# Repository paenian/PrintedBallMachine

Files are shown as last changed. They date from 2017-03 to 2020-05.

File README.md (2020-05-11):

The PrintedBallMachine!

Herein are some tips for working with the printed ball machine - making your own modules, first, and later making your own parts.

# Video!
https://www.youtube.com/watch?v=hsoqrZ5NXNs

# Rough Idea
The PBM is a marble machine that utilized pegboard for its vertical structure.  In order to make modular units, the pegboard is cut into 12" sections, with defined inlet and exit for linking together.  The machines are standardized on 5/8" steel ball bearings, because steel is satisfying.  This is the same size as the common glass marble, however there is much more variation in marbles than there are in ball bearings.

The Printed Ball Machine is designed in [OpenSCAD](http://www.openscad.org/), the programmer's solid modeler.

# Common Parts (vitamins, in the RepRap lingo - stuff you'll need to buy)
* Pegboard - 1" holes, 1/4" thick.  This is the 'heavy duty' pegboard, usually just brown hardboard.  Thinner stuff works, but not as well.  Generally sold in 2 foot by 4 foot sections - for modules, cut to 12" square.  Available at Home Depot/Lowes type stores - and they'll cut it if you ask nicely.
  * [home depot](https://www.homedepot.com/p/Triton-1-4-in-x-1-8-in-Heavy-Duty-Brown-Pegboard-Wall-Organizer-Set-of-4-TPB-4BR/205196091)
* 5/8" Steel Ball Bearings - I get mine from McMaster Carr, but anything'll work.
* Pololu plastic gear motors - I standardized on this motor because it fits nicely in a 1" space, has a right-angle drive and decent torque, plus runs off 5v easily.
  * [Pololu Plastic Gearmotor](https://www.pololu.com/product/1120)
  * You can get less-geared versions for faster motors, too.
* USB Charger and Cables
  * The motors are nominally 6v, but run fine (a little slower) at 5v - so we cut up old or cheap USB cables to power them.
  * You can also buy USB splitters, to minimize the number of chargers needed - two motors per amp is safe, in practice 4 seems to work fine.
* M3x12mm flat-head screws - two to hold each motor on, no tapping :-)
* #3 by 3/8" flat wood screws - used to hold parts onto the motor, fits perfectly into its D-shaft, no tapping.
* 12" x 3/8" wooden dowels - to make a single-module with ball recirculation.

# Getting Started
To get started, you need a pegboard, a motor or two, and a 3D printer. To make life easier, we've broken the parts into modules - 12"x12" units that can be linked together.  A module is not complete; it requires the addition of feet and a ball return option - either wooden dowels to recirculate around the back, straight peg clamps to attach it to another adjacent module, 180 degree ball returns to mate it to a second module behind it or 90 degree ball returns to turn it into a square.

I think the best unit is actually two modules back-to-back - these can be recirculated simply, and joined by removing the recirculators and lining them up.  There are three ready modules:

[Stair Lifter Module](stair_lifter_module)

[Bearing Lifter Module](bearing_lifter_module)

[Screw Lifter Module](screw_lifter_module)

# Common Parts for Printing: The Standard Module
There are many standard parts in the [parts](parts) subfolder; in general modules will utilize many of these common components, i.e. feet, handles, pegs, ball returns, and simple sloped modules.  Then, each module will have a small number of largely unique parts, for its lifting and transporting mechanism.  A completed module will have a parts list divided into unique and standard, so it's easy to print and assemble it all :-)

# Tracks
The [tracks](tracks) subfolder contains a set of simple track modules, which can all carry the marble a certain number of spaces while dropping one space.  These can be used in modules directly, as glue logic basically - if you don't want to design a crazy exotic drop, or need a long ramp, see here.

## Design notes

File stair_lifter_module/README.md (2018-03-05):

# Stair Lifter!

A marble machine module that uses a stair-step mechanism on a cam.  The actual lifter consists of three parts:
# Unique Parts
* sl_inlet.stl - The back set of stairs, doubles as the outlet.  Recommended print in PLA
* sl_stairs.stl - The front, moving set of stairs - rides up and down on the cam.  Again, recommend PLA for easy sliding.
* sl_cam.stl - Oval to lift and lower the stairs - attaches to the motor which is mounted on the sl_inlet.

The module is finished off with a wide slope to drop the ball bearings back down:
# Track
* wide_slope.stl - found in the [tracks](../tracks) folder

## Assembly
To complete the assembly, you'll need a bunch of printed pegs, feet, and one finishing style.

### Finishing
* Straight Clamps - connect to module left and right
* Dowel Returns - recirculate balls back to ourselves
* 180 degree - link two modules
* 90 degree - turn the corner

## Double Module
marble enters in at mid-height, exits the same height.  Requires another similar module and two ball_return_180.stl from the [parts](../parts) folder.

 Uniques
* sl_inlet.stl - The back set of stairs, doubles as the outlet.  Recommended print in PLA
* sl_stairs.stl - The front, moving set of stairs - rides up and down on the cam.  Again, recommend PLA for easy sliding.
* sl_cam.stl - Oval to lift and lower the stairs - attaches to the motor which is mounted on the sl_inlet.

### Tracks
* wide_slope.stl - found in the [tracks](../tracks) folder

### Standard Parts
* 2 stand.stl - and note that the feet are on columns 2 and 12, counting from 1 to 12, i.e. we skip the first column.  Also, the longer part of the foot is to the front of the module.
* 13 peg_tpu.stl - printed in TPU, or use the PETG files printed in PETG.
  * 4 for the legs, 4 for the wide slope, 5-ish for the stair inlet.

### Vitamins
* 12"x12" square of 1/4" pegboard
* 2 M3x12mm flat-head screws - to attach the motor
* 1 #3 by 3/8" flat-head wood screws - to attach the sl_cam.stl to the motor shaft
* 1 [Pololu Plastic Gearmotor](https://www.pololu.com/product/1120)
* USB charger/cable/5v supply
  * Note that the motor can turn in either direction in this module.

## Linking Double Modules
To link two standard double modules, double the parts above or use a different module, and add: 

## Parts
* 2 ball_return_180.stl - turn the balls around at the ends
* 6 peg_tpu.stl - to hold the ball returns on
* 1 double_handle.stl - to rigidly affix the two pegboards to eachother
* 2 M5x60mm screws - attach the handle
* 2 M5 nuts
* 4 M5 washers

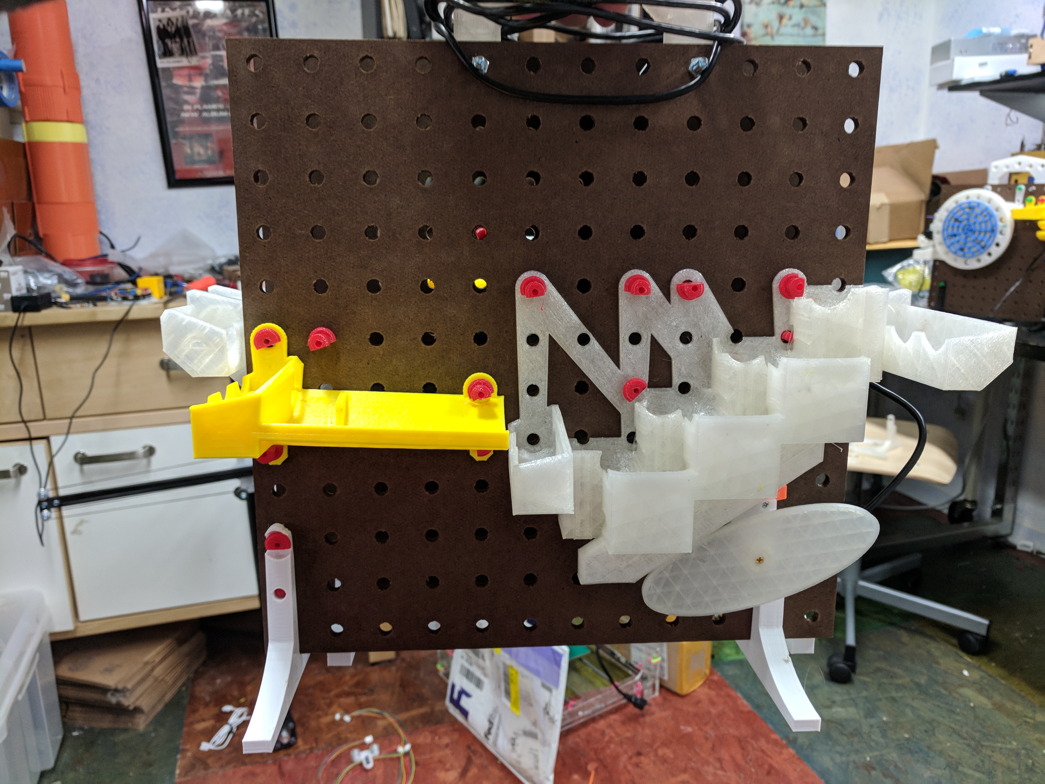
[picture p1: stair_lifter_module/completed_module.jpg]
Picture of the finished ball machine module Here's a completed double module, ready to recirculate.


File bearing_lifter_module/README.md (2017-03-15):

# Bearing Lifter
This is a lifter module, utilizing a print-in-place bearing.

Mechanical Parts:
1 motor
2 M5 screws and nuts for the handle
2 M3 screws to attach the motor
1 M3 screw to attach the guard

Parts to Print:
1 * bl_inlet.stl - marbles go in; also mounts the motor & bearing.
1 * bl_outlet.stl - marbles come out.
1 * bl_lift_gear.stl - the big bearing
1 * bl_drive_gear.stl - drive gear, attaches to the motor
1 * bl_guard.stl - finger guard, cuz the bearing's got ouchy torque
1 * bl_spiral.stl - a simple spiral drop.

Standard Parts
1 * stand_left.stl - pegboard stand
1 * stand_right.stl - pegboard stand
1 * handle.stl - to carry the pegboard
1 * breturn_inlet.stl - ball return!
1 * breturn_outlet.stl - ball return!
2 * breturn_peg.stl - special peg for the return
3 * peg_1x.stl - 1" peg
4 * peg_2x.stl - 2" peg
4 * peg_3x.stl - 3" peg

Notes:
Motor direction matters!
bl_inlet uses long pegs where it can.
You need a sideways support peg for the bl_outlet, under the fang-like curve.

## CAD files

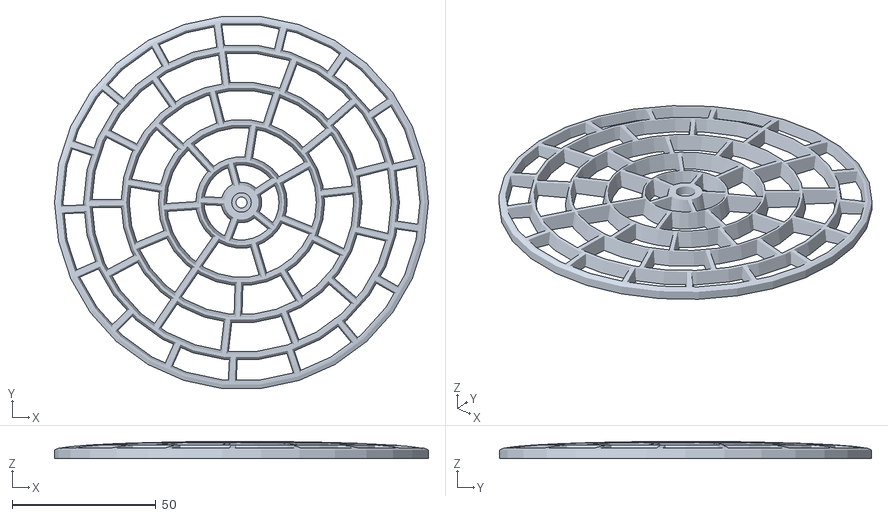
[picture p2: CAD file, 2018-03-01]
bearing_lifter_module/bl_guard.stl
130.0 x 129.3 x 5.98

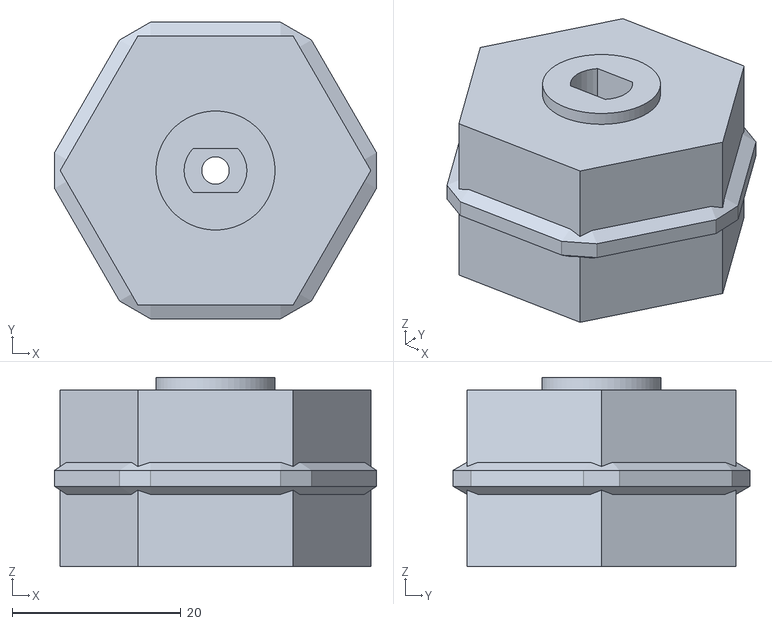
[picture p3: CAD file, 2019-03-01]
chain_lifter/cl_drive_gear.stl
38.1 x 35.2 x 22.4

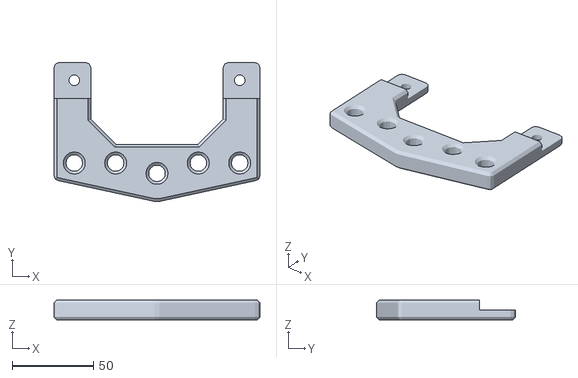
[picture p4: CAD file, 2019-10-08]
parts/handle.stl
126.5 x 85.2 x 12.2

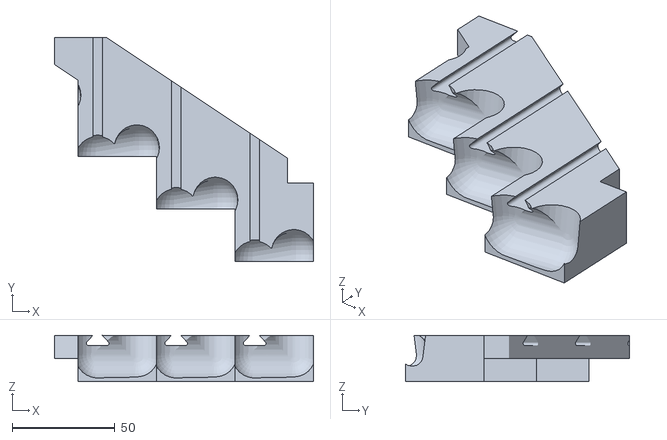
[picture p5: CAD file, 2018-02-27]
stair_lifter_module/sl_stairs.stl
125.7 x 108.5 x 22.4

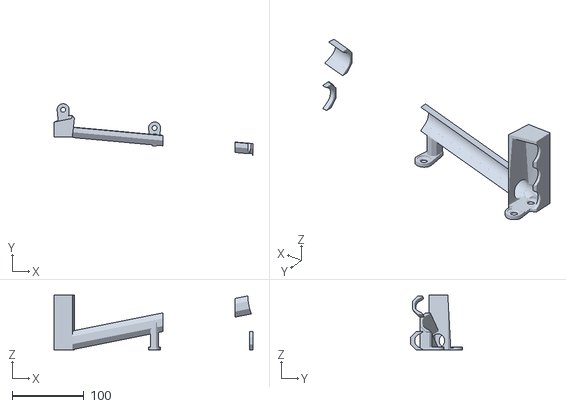
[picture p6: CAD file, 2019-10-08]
tracks/offset_slope_6.stl
276.4 x 71.6 x 76.2

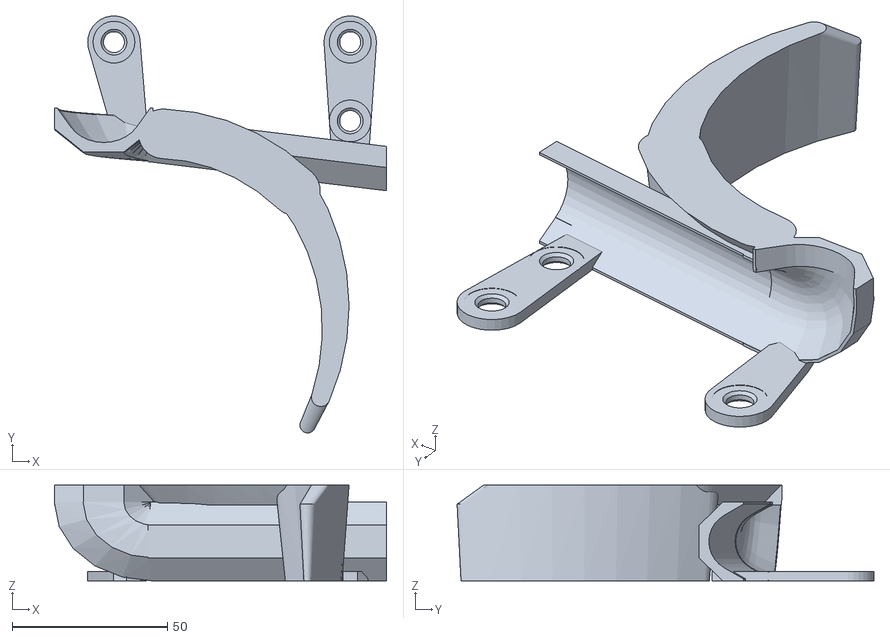
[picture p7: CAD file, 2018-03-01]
bearing_lifter_module/bl_outlet.stl
107.1 x 134.5 x 30.9

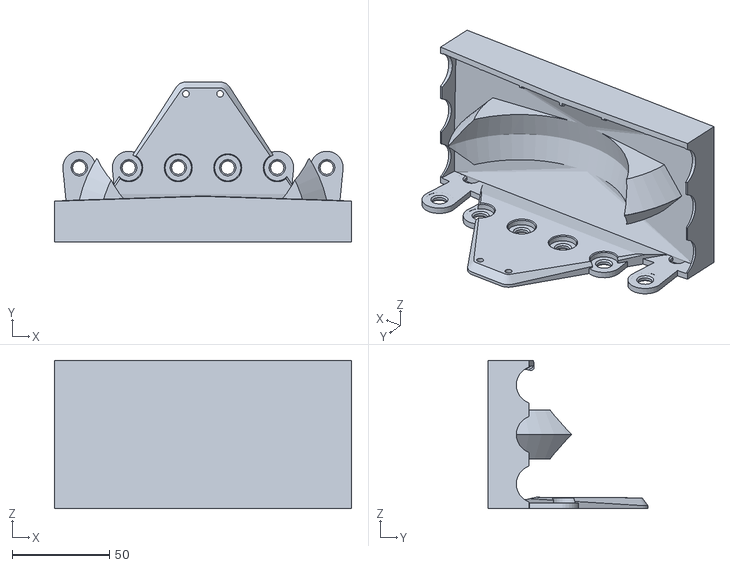
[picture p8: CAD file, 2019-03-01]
chain_lifter/cl_inlet.stl
152.4 x 82.1 x 76.2

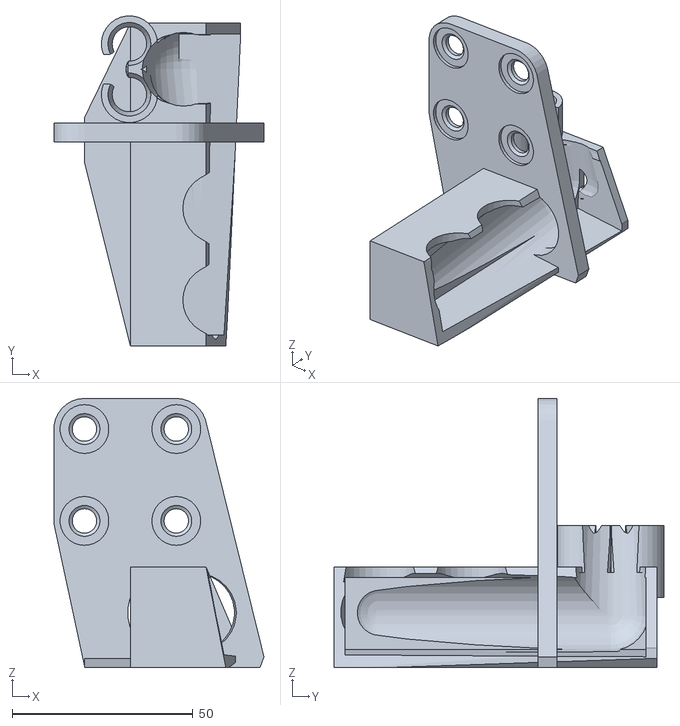
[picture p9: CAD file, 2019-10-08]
parts/ball_return_inlet_2.stl
58.1 x 91.2 x 74.4

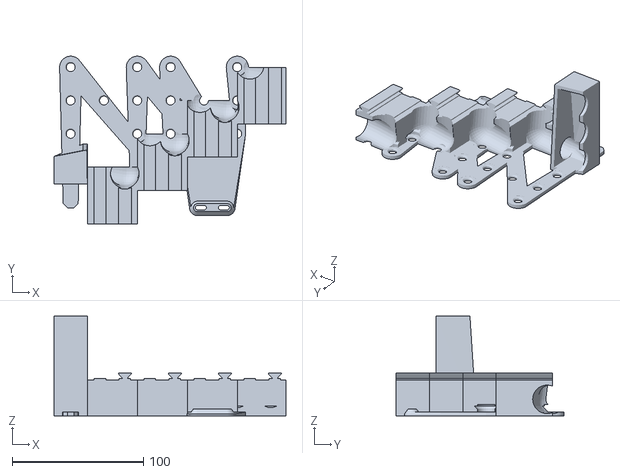
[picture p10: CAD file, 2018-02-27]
stair_lifter_module/sl_inlet.stl
176.8 x 127.7 x 76.2

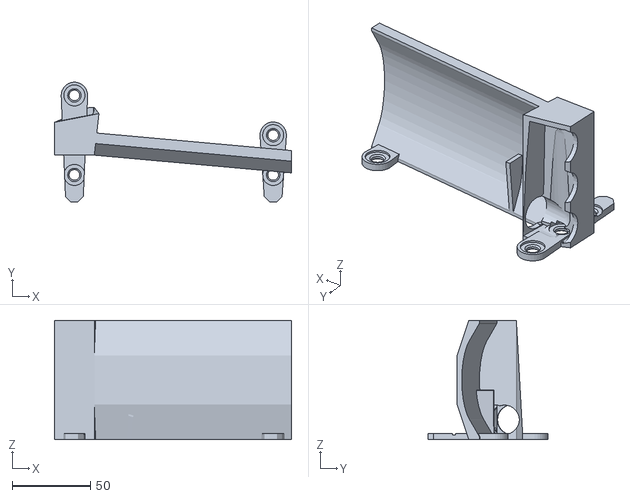
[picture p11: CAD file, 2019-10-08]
tracks/wide_slope_6.stl
151.4 x 76.4 x 76.2

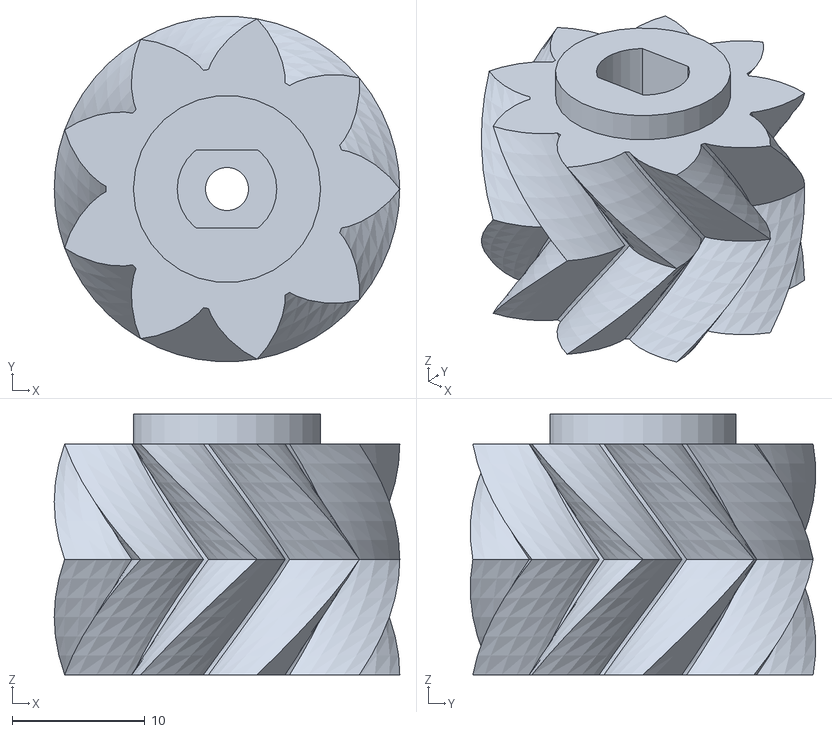
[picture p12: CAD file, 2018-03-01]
bearing_lifter_module/bl_drive_gear.stl
26.0 x 26.0 x 19.6

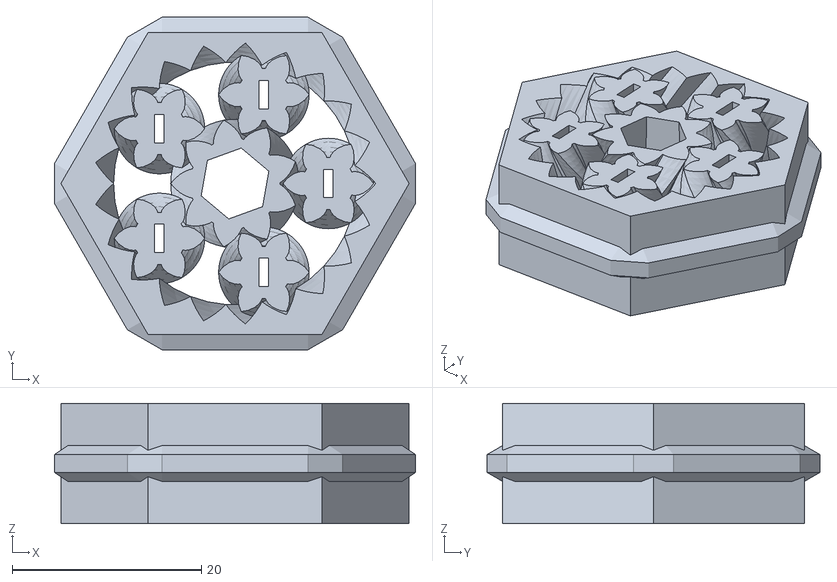
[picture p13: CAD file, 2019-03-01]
chain_lifter/cl_idler_gear.stl
38.1 x 35.2 x 12.7

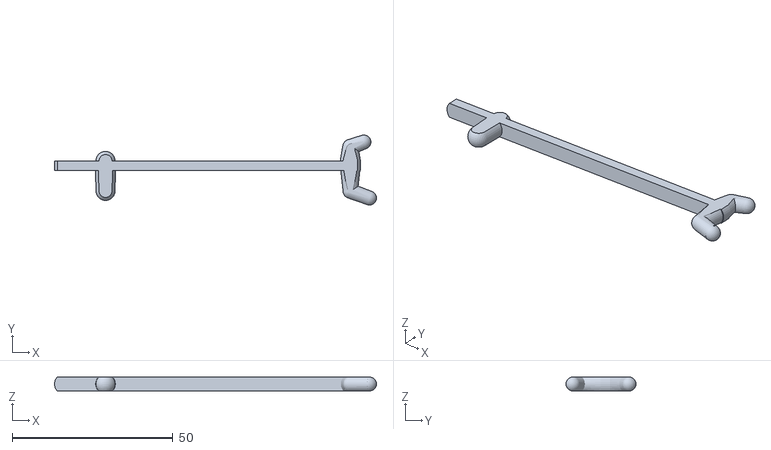
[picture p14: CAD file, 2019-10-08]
parts/peg_3l.stl
100.2 x 21.8 x 4.35

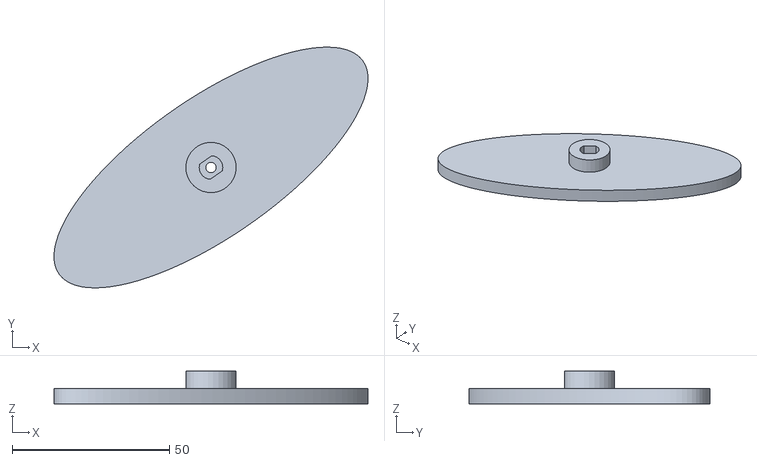
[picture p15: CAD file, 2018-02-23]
stair_lifter_module/sl_cam.stl
99.8 x 76.5 x 10.5

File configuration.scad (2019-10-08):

in = 25.4;

$fn=30;

slop = .2;

//pegboard variables
peg_rad = 1/4*in/2;
peg_sep = 1*in;
peg_thick = 1/4*in;
peg_cap_rad = .25*in;

wall=3;

//used for the ball return
dowel_rad = (3/8)/2*in;
dowel_sep = 16-2;
dowel_holder_height = 20;
rear_gap = 1.25*in;

//ball variables
ball_rad = 5/8*in/2;

//track_rad = ball_rad+1+.5;  //this is the minimum size, I think
track_rad = in/2-wall; //this makes the track an inch wide

//inlet variables
inlet_x = in;
inlet_y = in*2;
inlet_z = in*1;
INLET_HOLE = 1;
INLET_SLOT = 2;
INLET_NONE=0;
NONE = 0;
NORMAL = 0;
REVERSE = 5;
SWITCH = 8;
FLIP_FLOP = 9;
CENTER = 4;

PEG_PIN = 1;
PEG_HOOK = 2;
PEG_LOWER_HOOK = 3;
PEG_NONE = 0;

m3_rad = 3/2 + slop;
m3_cap_rad = 6/2 + slop;
m3_nut_rad = 6.6/2;


m5_nut_rad = 8.79/2;
m5_sq_nut_rad = (8*sqrt(2)+slop/2)/2;
m5_nut_rad_laser = 8.79/2-.445;
m5_nut_height = 4.7;
m5_rad = 5/2+slop;
m5_rad_laser = 5/2-.1;
m5_cap_rad = 10/2+slop;
m5_cap_height = 3;
m5_washer_rad = 11/2+slop;

//pin variables
pin_tolerance = .25;
pin_rad = 4;
pin_lt = 1;

//motor shaft variables
motor_dflat=.9;
motor_shaft=7+slop/4;
motor_bump=1.5;

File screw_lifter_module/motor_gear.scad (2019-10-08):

// Differential planetary drive (customizable)

use <write/Write.scad>



in = 25.4;

//this should be the torque transfer diameter
//note that the sun can be smaller :-)
%cylinder(r=in*1.5, h=50);
%cylinder(r=bearing_rad, h=60);

rod_rad = 15/2+.25;
screw_rad = in*2.5+.75;
rod_ring_rad = screw_rad+rod_rad+.5;
bearing_rad = 35/2+.25;
bearing_thick = 11.75;
joint = 15;
    
//these are the pegs to secure the stationary ring gear
for(i=[0:360/3:359]) rotate([0,0,i]) translate([rod_ring_rad,0,0])
    %cylinder(r=rod_rad, h=50);

//assembly();
choose(export);

// choose the object to render
export=1;// [0:Input,1:Output]
// outer diameter of ring
D=in*5.25;
//chamfer radius on the gears
chamfer = 3;
// thickness
T=19;
// clearance between gear teeth
tol=0.25;
// vertical clearance
vtol=0.5;
number_of_planets=5;
number_of_teeth_on_planets=16;
approximate_number_of_teeth_on_sun=29;
// difference in teeth on ring gears
delta=-1;
// number of teeth to twist across
nTwist=1;
// pressure angle
P=30;
// width of hexagonal hole
w=6.7;

DR=2/PI;// maximum depth ratio of teeth

m=round(number_of_planets);
np=round(number_of_teeth_on_planets);
nsa=approximate_number_of_teeth_on_sun;
ka=round(2/m*(nsa+np));
k= ka*m%2!=0 ? ka+1 : ka;
ns=k*m/2-np;
echo(ns);
nr=ns+2*np;
nr2=nr+delta;
np2=np+delta;
pitchD=0.9*D/(1+depth_diameter(nr,P,DR));
pitch=pitchD*PI/nr;
echo(pitch);
helix_angle=atan(2*nTwist*pitch/T);
echo(helix_angle);

phi=$t*360;
R1=(1+nr/ns);// sun to planet-carrier ratio
R2=-nr2*np/(ns+np)/delta;// planet-carrier to ring ratio
R=R1*R2;
echo(R);

module choose(i){
if(i==0) planetary();
else ring();
}

module plate(){
translate([D+1,0,0])planetary();
translate([-D-1,0,0])ring();
}

module assembly(){
planetary();
translate([0,0,3*T/2+1+3*vtol])rotate([180,0,phi/R2-turn(nr2,pitch,helix_angle,vtol)])render()ring();
}

module ring()
difference(){
	union(){
		difference(){
			cylinder(r=D/2*nr2/nr-1,h=T/2+3,$fn=100);
			translate([0,0,3])gear(nr2,pitch,P,DR,-tol,helix_angle,T/2+0.2);
		}
		cylinder(r=0.9*innerR(ns,pitch,P,tol,DR),h=T/2+1);
		cylinder(r=w/3,h=T/2+1+3*vtol);
	}
	translate([0,0,-1])cylinder(r=w/sqrt(3),h=T,center=true,$fn=6);
	for(i=[1:6])rotate([0,0,i*60])translate([pitchD/2*(ns+np)/nr-3.5,0,0])
		cylinder(r=innerR(np2,pitch,P,tol,DR)+2,h=11,center=true);
    
    //bearing support
    translate([0,0,-.5]) cylinder(r=bearing_rad, h=T*7, $fn=6, center=true);
    translate([0,0,0]) cylinder(r=bearing_rad, h=bearing_thick, center=true);
    
    //holes to lock to the screw
    for(i=[30:360/6:359]) rotate([0,0,i]) translate([22,0,0]) {
        cylinder(r=3.4/2, h=T*2, center=true, $fn=30);
        translate([0,0,2]) cylinder(r=4, h=T*2, $fn=30);
    }
}

module planetary()
translate([0,0,T/2]){
	//ring gear
    difference(){
		cylinder(r=D/2,h=T,center=true,$fn=100);
		herringbone(nr,pitch,P,DR,-tol,helix_angle,T+0.2);
		
        translate([0,0,-T/2]) rotate_extrude(){
            translate([pitchR(nr,pitch)-rackDepth(pitch,P)/2+max(-tol,0), 0, 0]) circle(r=chamfer, $fn=4);
        }
        //these are the pegs to secure the stationary ring gear
        for(i=[0:360/3:359]) rotate([0,0,i]) translate([rod_ring_rad,0,0])
            cylinder(r=rod_rad, h=T*5, center=true);
        
        //let's put some zip ties in there for good measure
        for(i=[0:360/3:359]) rotate([0,0,i]) translate([rod_ring_rad,0,0]) {
            rotate_extrude(){
                translate([rod_rad+4, 0, 0]) square([2,4], center=true);
            }
        }
	}
    
    //sun gear
	rotate([0,0,(np+1)*180/ns+phi*R1])
	difference(){
		mirror([0,1,0])
			herringbone(ns,pitch,P,DR,tol,helix_angle,T);
		translate([0,0,-1])cylinder(r=w/sqrt(3),h=T,center=true,$fn=6);
        
        translate([0,0,-T/2]) rotate_extrude(){
            translate([pitchR(ns,pitch)+rackDepth(pitch,P)/2+max(-tol,0), 0, 0]) circle(r=chamfer, $fn=4);
        }
        for(i=[30:360/6:359]) rotate([0,0,i]) translate([22,0,0]) {
            cylinder(r=3.4/2, h=T*2, center=true, $fn=30);
        }
        
        //bearing support
        translate([0,0,-.5]) cylinder(r=bearing_rad, h=T*7, $fn=6, center=true);
        translate([0,0,-T/2]) cylinder(r=bearing_rad, h=bearing_thick, center=true);
	}
	for(i=[1:m])rotate([0,0,i*360/m+phi])translate([pitchD/2*(ns+np)/nr,0,0])
		rotate([0,0,-phi*(ns+np)/np-phi]){
			difference(){
				rotate([0,0,i*ns/m*360/np])herringbone(np,pitch,P,DR,tol,helix_angle,T+3*vtol);
				translate([0,0,-D/2-T/2])cube(D,center=true);
                
                translate([0,0,-T/2]) rotate_extrude(){
                    translate([pitchR(np,pitch)+rackDepth(pitch,P)/2+max(-tol,0), 0, 0]) circle(r=chamfer, $fn=4);
                }
			}
			rotate([0,0,i*ns/m*360/np-turn(np,pitch,helix_angle,vtol)])translate([0,0,T/2+vtol-0.01])
				cylinder(r=outerR(np,pitch,P,tol,DR)-tol,h=vtol+0.02,$fn=np);
			rotate([0,0,-i*nr2/m*360/np2])translate([0,0,T/2+2*vtol])
				difference(){
                    gear(np2,pitch,P,DR,tol,helix_angle,T/2);
                    translate([0,0,T/2]) rotate_extrude(){
                    translate([pitchR(np,pitch)+rackDepth(pitch,P)/2+max(-tol,0), 0, 0]) circle(r=chamfer, $fn=4);
                }
                }
		}
}

module monogram(h=1)
linear_extrude(height=h,center=true)
translate(-[3,2.5])union(){
	difference(){
		square([4,5]);
		translate([1,1])square([2,3]);
	}
	square([6,1]);
	translate([0,2])square([2,1]);
}

module herringbone(
	number_of_teeth=15,
	circular_pitch=10,
	pressure_angle=20,
	depth_ratio=2/PI,
	clearance=0,
	helix_angle=0,
	gear_thickness=5){
union(){
	gear(number_of_teeth,
		circular_pitch,
		pressure_angle,
		depth_ratio,
		clearance,
		helix_angle,
		gear_thickness/2);
	mirror([0,0,1])
		gear(number_of_teeth,
			circular_pitch,
			pressure_angle,
			depth_ratio,
			clearance,
			helix_angle,
			gear_thickness/2);
}}

module gear (
	number_of_teeth=15,
	circular_pitch=10,
	pressure_angle=20,
	depth_ratio=2/PI,
	clearance=0,
	helix_angle=0,
	gear_thickness=5,
	flat=false){
twist=turn(number_of_teeth,circular_pitch,helix_angle,gear_thickness);

flat_extrude(h=gear_thickness,twist=twist,flat=flat)
	gear2D (
		number_of_teeth,
		circular_pitch,
		pressure_angle,
		depth_ratio,
		clearance);
}

module flat_extrude(h,twist,flat){
	if(flat==false)
		linear_extrude(height=h,twist=twist,slices=twist/6)child(0);
	else
		child(0);
}

module gear2D (
	number_of_teeth,
	circular_pitch,
	pressure_angle,
	depth_ratio,
	clearance){
pitch_radius = pitchR(number_of_teeth,circular_pitch);
base_radius = pitch_radius*cos(pressure_angle);
depth = rackDepth(circular_pitch,pressure_angle);
max_radius = pitch_radius+depth/2+max(-clearance,0);
//outer_radius = pitch_radius+depth_ratio*circular_pitch/2-clearance/2;
outer_radius = outerR(number_of_teeth, circular_pitch, pressure_angle, clearance, depth_ratio);
//root_radius1 = pitch_radius-depth/2-clearance/2;
//root_radius = (clearance<0 && root_radius1<base_radius) ? base_radius : root_radius1;
//inner_radius = max(root_radius,pitch_radius-depth_ratio*circular_pitch/2-clearance/2);
inner_radius = innerR(number_of_teeth, circular_pitch, pressure_angle, clearance, depth_ratio);
min_radius = max(base_radius,inner_radius);
backlash_angle = clearance/(pitch_radius*cos(pressure_angle)) * 180 / PI;
pitch_point = involute (base_radius, involute_intersect_angle (base_radius, pitch_radius));
tip_angle = atan2(pitch_point[1], pitch_point[0]) + 90/number_of_teeth - backlash_angle/2;

intersection(){
	circle($fn=number_of_teeth*2,r=outer_radius);
	union(){
		rotate(90/number_of_teeth)
			circle($fn=number_of_teeth*2,r=inner_radius);
		for (i = [1:number_of_teeth])rotate(i*360/number_of_teeth){
			halftooth (
				base_radius,
				min_radius,
				max_radius,
				tip_angle);		
			mirror([0,1])halftooth (
				base_radius,
				min_radius,
				max_radius,
				tip_angle);
		}
	}
}}

module halftooth (
	base_radius,
	min_radius,
	max_radius,
	tip_angle){
index=[0,1,2,3,4,5];
start_angle = max(involute_intersect_angle (base_radius, min_radius)-5,0);
stop_angle = involute_intersect_angle (base_radius, max_radius);
angle=index*(stop_angle-start_angle)/index[len(index)-1];
p=[[0,0],
	involute(base_radius,angle[0]+start_angle),
	involute(base_radius,angle[1]+start_angle),
	involute(base_radius,angle[2]+start_angle),
	involute(base_radius,angle[3]+start_angle),
	involute(base_radius,angle[4]+start_angle),
	involute(base_radius,angle[5]+start_angle)];

difference(){
	rotate(-tip_angle)polygon(points=p);
	square(2*max_radius);
}}
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

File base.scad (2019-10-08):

include<configuration.scad>
use <pins.scad>
%pegboard(size = [12,12]);

part = 2;

//bare inlet
if(part == 0)
    rotate([-90,0,0]) inlet();

if(part == 1)
    rotate([-90,0,0]) inlet(length=2);

if(part == 2)
    rotate([-90,0,0]) inlet(length=3);

if(part == 3)
    rotate([-90,0,0]) slope_module(size = [2, -.45]);

if(part == 4)
    rotate([-90,0,0]) slope_module(size = [3, -.45]);

if(part == 5)
    rotate([-90,0,0]) slope_module(size = [4, -.45]);

if(part == 6)
    rotate([-90,0,0]) slope_module(size = [5, -.45]);

if(part == 7)
    rotate([-90,0,0]) offset_slope_module(size = [3, -.45]);

if(part == 8)
    rotate([-90,0,0]) offset_slope_module(size = [4, -.45]);

if(part == 9)
    rotate([-90,0,0]) offset_slope_module(size = [5, -.45]);

if(part == 10)
    rotate([-90,0,0]) wide_slope_module(size = [3, -.45]);

if(part == 11)
    rotate([-90,0,0]) wide_slope_module(size = [4, -.45]);

if(part == 12)
    rotate([-90,0,0]) wide_slope_module(size = [5, -.45]);


if(part == 0)
    demo_panel();

//the size is the X and Y number of holes in the peg board.
//This is meant to be used as a visual reference when designing your module.
module pegboard(size = [12,6]){
    difference(){
        cube([size[0]*in, peg_thick, size[1]*in]);
        
        translate([-.5*in,0,-.5*in]) 
        for(i=[1:size[0]])
            for(j=[1:size[1]])
                translate([i*peg_sep, 0, j*peg_sep]) rotate([90,0,0]) cylinder(r=peg_rad, h=in, center=true);
    }
}

module demo_panel(){
    union(){
        pegboard(size = [12,12]);
        translate([-peg_sep*4,0, peg_sep*4]) slope_module(size = [3,-.5]);
        translate([peg_sep*12,0,peg_sep*5]) slope_module();
    }
}

//A sample module which uses the inlet to roll balls down a chute.
module slope_module(size = [4, -.5], width=3, inlet = NORMAL){
    difference(){
        union(){
            if(inlet == NORMAL){
                inlet(height=3, width=width);
            }
            if(inlet == REVERSE){
                translate([peg_sep,0,0]) mirror([1,0,0]) inlet(height=3, width=width, outlet = REVERSE);
            }
            
            translate([in,0,in*2]) track(rise=(size[1]*1.1)*in, run=(size[0]*1.1)*in, solid=1, end_angle=0);
            hanger(solid=1, hole=[floor(size[0])+1,3], drop = -size[1]*in);
        }
        //hole in the inlet
        *translate([in,0,in*2]) track(rise=size[1], run=size[0], solid=-1, hanger=0, extra_len=in-wall*1.5);

		  //cut the end flat
		  translate([50+in*size[0]+in-1,0,in*2]) cube([100,100,100], center=true);
        
         hanger(solid=-1, hole=[floor(size[0])+1,3], drop = in/2);
    }
}

//A sample module which uses the inlet to roll balls down a wide, rolly chute
module wide_slope_module(size = [4, -.5], width=3){
    height = 3;
    difference(){
        union(){
            inlet(height=height, width=width);
            //beefy bottom for more slopey
            translate([0,-in*width,in*2]) cube([in,in*width,in*.55]);
            
            %translate([in*1.45, -in/2, in*2.5]) sphere(r=ball_rad+wall/2);
            
            //flapper to kick it downslope
            intersection(){
                translate([in+ball_rad*2+wall*2.5, -in*1.25, in*2]) rotate([0,0,5]) cube([wall, in*1.25, in]);
                hull() translate([in,0,in*2]) scale([1,width,1]) track(rise=(size[1]*1.1)*in, run=(size[0]*1.1)*in, solid=1, end_angle=0);
            }   
            
            translate([in,0,in*2]) scale([1,width,1]) track(rise=(size[1]*1.1)*in, run=(size[0]*1.1)*in, solid=1, end_angle=0);
            
            hanger(solid=1, hole=[floor(size[0])+1,3], drop = -size[1]*in+in);
            hanger(solid=1, hole=[1,4], drop = -size[1]*in+in*2);
        }
        //inlet exit
        hull(){
            translate([in/2, -in/2, (height-.2)*in]) sphere(r=ball_rad+wall/2);
            translate([in*1.5, -in/2, (height-.3)*in]) sphere(r=ball_rad+wall/2);
        }
        
        hull(){
            translate([in/2, -in/2, (height-.2)*in]) sphere(r=ball_rad+wall/2);
            translate([in/2, -width*in+in/2, (height-.1)*in]) sphere(r=ball_rad+wall/2);
        }

          //cut the end flat
          translate([100+in*size[0]+in-1,0,in*2]) cube([200,200,200], center=true);
        
         //hanger(solid=-1, hole=[floor(size[0])+1,3], drop = in/2);
        
        for(i=[2:1:4]){
            hanger(solid=-1, hole=[floor(size[0])+1,i], drop = -size[1]*in+in);
            hanger(solid=-1, hole=[1,i], drop = -size[1]*in+in*2);
        }
    }
}

//A sample module which uses the inlet to roll balls down a chute.
module offset_slope_module(size = [4, -.5], offset=1){
    inset = wall;
    z_out = offset*in*2;
    
    
    difference(){
        union(){
            inlet(height=3, length=1);
            
            translate([in-inset,0,in*2])  difference(){
                track(rise=(size[1]*2)*in, run=(size[0]*2)*in, z_out=z_out, solid=1, end_angle=0);
                //flatten the front
                translate([-25+inset,-25,0]) cube([50,50,50], center=true);
            }
            hanger(solid=1, hole=[floor(size[0])+1,3], drop = in*.75);
            
            //lower end support
            hull(){
                translate([(floor(size[0])+.5)*in,0,in*2.5-in*.75]) rotate([90,0,0]) rotate([0,0,22.5]) cylinder(r=wall*2, h=in*1.5, $fn=8);
                translate([(floor(size[0])+.5)*in,0,in*2.5-in*.55]) rotate([90,0,0]) rotate([0,0,22.5]) cylinder(r=wall*2, h=in*1.5, $fn=8);
            }
            
        }
        
        translate([in-inset,0,in*2]) difference(){
            track(rise=(size[1]*2)*in, run=(size[0]*2)*in, z_out=z_out, solid=-1, end_angle=0);
            //flatten the front
            translate([0,-25,track_rad+wall]) cube([50,50,50], center=true);
        }

		 //cut the end flat
		 translate([50+in*size[0]+in-1,0,in*2]) cube([100,200,200], center=true);
        
         hanger(solid=-1, hole=[floor(size[0])+1,3], drop = in*.75);
    }
}

//a module to turn the marbles around.
module reverse_module(size = [4, -.5]){
    difference(){
        union(){
            inlet(height=3, hanger_height=1);
            
            translate([0,0,in*2]){
                translate([in,0,0]) track(rise=(size[1]*.5)*in, run=(size[0]*1)*in, solid=1, end_angle=90);
                difference(){
                    translate([-.25*in,-in*2,size[1]*in]) mirror([0,1,0]) track(rise=(size[1]*-.5)*in, run=(size[0]+1.25)*in, solid=1, end_angle=90);
                    //gotta cut the end flat
                    translate([-49,0,in*2]) cube([100,200,100], center=true);
                }
            }
            
            //support
            translate([peg_sep/2,-peg_sep,peg_sep*1.5]) cube([peg_sep-2,wall/2,peg_sep], center=true);
            
            hanger(solid=1, hole=[size[0],4], drop = in*1.33);
        }
        //hole in the inlet
        //translate([in,0,in*2]) track(rise=size[1], run=size[0], solid=-1, hanger=0, extra_len=in-wall*1.5);

		  //cut the end flat
		  translate([50+in*size[0]+in,0,in*2]) cube([100,100,100], center=true);
        
        hanger(solid=-1, hole=[size[0],4], drop = in*1.33);
    }
}
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

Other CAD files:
tracks/simple_slope_6.stl
bearing_lifter_module/bl_spiral.stl
chain_lifter/cl_link_grab.stl
parts/ball_return_180.stl
base_module.scad
ball_return/ball_return.scad
bearing.scad
bearing_lifter_module/bearing_lifter.scad
bearing_lifter_module/bl_inlet.stl
bucket_lifter/bucket_lifter.scad
chain_lifter/chain_lifter.scad
chain_lifter/cl_link_plain.stl
clank_drop/clank_drop.scad
handle.scad
marbulous/marbulous.scad
parts/6_pegs.stl
parts/ball_return_90.stl
parts/ball_return_inlet_3.stl
parts/ball_return_joint.stl
parts/ball_return_outlet.stl
parts/double_handle.stl
parts/double_stand.stl
parts/peg.stl
parts/peg_1l.stl
parts/peg_2l.stl
parts/peg_petg.stl
parts/peg_petg_handle.stl
parts/peg_stand.stl
parts/peg_stand_m.stl
parts/peg_tpu.stl
parts/peg_tpu_double_handle.stl
parts/peg_tpu_handle.stl
parts/stand.stl
parts/straight_link.stl
peg.scad
pins2.scad
plinko_slope/plinko_slope.scad
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

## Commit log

2016-11-21 Resliced, minor tweaks to the handle mounts and feet.
    Working on the sl_inlet_2 - the inlet jams occasionally,
    I think the latest version will eliminate that.
    [ball_return.scad, bl_drive_gear.stl, bl_guard.stl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]
2016-11-23 Checked and ready, both lifters are.
    Paul
    [bearing_lifter.scad, bl_drive_gear.stl, bl_guard.stl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]
2016-11-29 Made a bigger clank drop, for my extended machine; larger tolerance bearing lifter bearings.
    [ball_return.scad, ball_return_3.stl, ball_return_peg.stl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]
2016-12-12 Made the ball-return space more parametric, upped it to 1.25 inches.
    Now you can set the rear ball return in the configuration.scad, which
    will affect the handle mounts, ball return inlet and outlet, and the
    stands.
    - Made a left and right stand, cuz it looks nicer mirrored
    - Adjusted the dowel mounts, for tighter fit
    - Moved the ball return inlet mount - so we can use 12" dowels
    - Added a dowel joiner
    - Some cleanup on part generation - more to come.
    [ball_return.scad, ball_return_joint.stl, ball_return_peg.stl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]
2017-01-11 More ball returns :-)
    [ball_return.scad, ball_return_3.stl, ball_return_inlet_2.stl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]
2017-03-08 Updating for the upcoming Maker Faire!
    [ball_return.scad, base.scad, big_slope.stl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]
2017-03-08 Updated the feet - slightly larger.
    [breturn_2inlet.stl, breturn_3inlet.stl, breturn_joint.stl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]
2017-03-09 Progress on the stair lifter.
    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
    [stair_lifter.scad]
2017-03-09 Still working on stair lifter.
    Need a guide for the moving stairs, and a cam for the motor.
    [base.scad, handle.scad, stair_lifter.scad]
2017-03-10 Stair lifter is almost done, well, printing tests.
    Still need to make a cam for the motor, but more worried about basic sliding first.
    Also started a plinko drop, because I think it'd look cool.
    [base.scad, handle.scad, handle.stl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]
2017-03-11 Finished stair lifter!
    It needs a little more polishing, but the initial lifter is up and running smoothly!
    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
    [sl_cam.stl, sl_inlet.stl, sl_stair.stl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]
2017-03-15 Working the bearing lifter to a fully print-ready state
    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
    [ball_return.scad, ball_return_joint.stl, base.scad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]
2017-05-21 Updated a lot of STLs, main changes to the ball return and bearing lifter inlet.
    Bugfix on curved track segments, no longer misaligned.
    [ball_return.scad, ball_return_inlet_2.stl, ball_return_inlet_3.stl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]
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2017-08-16 Added a pushpeg
    Thinking about easier production, instead of hanging bits off the
    pegboard, pin them in place. This puts the marble module flat
    against the pegboard, and is therefore incompatible with hangers.
    The idea would be to transition everything to pegs - for most parts
    that means the hanger can be shorter, but the ball return bits will
    need some re-thinking. Ideally these parts need to be easier to
    remove and re-add...
    [pins2.scad, pushpeg.scad, pushpeg.stl]
2017-08-16 Added an easy-remove version of the peg, which might not be suitable for all places.
    [pushpeg.scad, pushpeg_handle.stl]
2017-08-17 Updated the ball returns to sit flush - should make the machines all push-pin compatible.
    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
    [ball_return.scad, ball_return_inlet_2.stl, ball_return_outlet.stl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]
2017-08-23 Updated screw lifter so it can accommodate pegs
    [screw_lifter.scad, sl_inlet.stl]
2017-08-28 Playing with the pushpegs - these work really well, been using the 1.0 size.
    [pushpeg.scad, pushpeg_1.0.stl, pushpeg_1.1.stl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]
2017-12-27 Added a stand for pushpegs, and got the pegs working well in TPU.
    TPU pegs are easy to get in/out, but weaker than PETG; however the petg
    were just really a pain to use. Have to test these a bit more, but initial
    return is pretty nice. With a screw they're solid, without they don't work
    loose, but can be pulled out easily.
    [pushpeg.scad, pushpeg_stand.stl, pushpeg_tpu.stl]
2017-12-29 Removed a bunch of old STLs, working on new pegs, better compile scripts.
    [ball_return.scad, ball_return_inlet_2.stl, ball_return_inlet_3.stl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]
2018-01-02 Working on mating two machines back-to-back
    [ball_return.scad, ball_return_180_inlet_2.stl, ball_return_inlet_3.stl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]
2018-02-07 Starting on the 90 degree ball return.
    [ball_return.scad, ball_return_90_test.stl]
2018-02-11 Working on ball returns 180 degree to attach two units back to back, and 90 degree to make a square of units.
    [ball_return.scad, ball_return_90_test.stl, base.scad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]
2018-02-12 Updating everything for super-holey push pins
    [ball_return_180.stl, ball_return_90.stl, ball_return_inlet_2.stl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]
2018-02-19 Updated most of the main parts to have extra holes for insert pins.
    Makes it easier to do multi-side parts :-)
    [ball_return.scad, ball_return_180.stl, ball_return_180_inlet_3.stl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]
2018-02-23 Updating everything for pushpegs
    All STLs are going to be updated, as well as complete modules.
    [ball_return.scad, ball_return_180.stl, ball_return_180_inlet_2.stl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]
2018-02-27 Updated lots. Three lifters are good to print: bearing lifter screw lifter stair lifter
    [ball_return_180.stl, ball_return_90.stl, ball_return_inlet_2.stl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]
2018-02-27 left some debugging in :-/
    [screw_lifter.scad, sl_bowl_catch.stl, sl_bowl_drop.stl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]
2018-03-01 Updated the bearing lifter - proper module now
    [ball_return.scad, bearing_lifter.scad, bl_drive_gear.stl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]
2018-03-01 ok NOW it's a module
    [bearing.scad, bearing_lifter.scad, bl_drive_gear.stl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]
2018-03-05 Updated the screw lifter files
    [clank_drop.scad, configuration.scad, screw_lifter.scad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]
2018-03-06 Updated the screw lifter - had the old screw in there.
    [screw_lifter.scad, sl_bowl_catch.stl, sl_bowl_drop.stl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]
2018-06-01 updated STLs, chain lifter
    [ball_return_180.stl, ball_return_90.stl, ball_return_inlet_2.stl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]
2019-01-25 updating the screw lifter - new idea to prevent jams
    much larger screw, with a bucket cross section. It will need a
    screw guide that also has a marble stop sticking into the ball
    path.
    [screw_lifter.scad, test_screw.stl]
2019-01-25 Updated the test screw, chain lifter?
    apparently I worked on it at some point :-0
    [chain_lifter.scad, cl_drive_gear.stl, cl_idler_gear.stl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]
2019-01-29 Updated screw lifter - less jamming
    [base.scad, bowl_drop.scad, screw_drop.scad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]
2019-02-11 Added some lifters - working on the giant pegboard lifter.
    [base.scad, configuration.scad, double_pegboard_lifter.stl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]
2019-02-18 Updated the lifter - everything should be final version.
    Gotta play with the other parts, and do some cleanup.
    [screw_lifter.scad, sl2_extend_guide.stl, sl2_extend_peg_screw.stl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]
2019-02-20 Made the pegboard lifter taller, with more slope.
    The marbles went in, but it was a bit laconic. I need pep in my
    useless machines! You will run, you will like it and you will
    continue until the electricity fails.
    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
    [double_pegboard_lifter.stl, screw_lifter.scad, sl2_extend_peg_screw.stl]
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2019-03-01 Added a top for the big screw lifter
    [screw_lifter.scad, sl2_extend_top.stl]
2019-03-02 Widened the holes on the top plate
    [screw_lifter.scad, sl2_extend_top.stl]
2019-03-17 Added a base for the 2" lifter
    ad a plug to connect the bottom segment to the bearing
    [screw_lifter.scad, two_inch_screw.stl, two_inch_screw_base.stl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]
2019-04-08 Working on the 2" screw
    [diffplanet1.scad, screw_lifter.scad, two_inch_screw_boxpeg.stl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]
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2019-04-22 Updated the two inch screw lifter so it can take a little motor.
    Future work will be making a gear reduction that a wind turbine
    can handle :-)
    [bearing.scad, bearing_lifter.scad, configuration.scad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]
2019-04-22 Updated the motor driver
    [screw_lifter.scad, two_in_motor_collar.stl, two_inch_screw_gears.scad]
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
